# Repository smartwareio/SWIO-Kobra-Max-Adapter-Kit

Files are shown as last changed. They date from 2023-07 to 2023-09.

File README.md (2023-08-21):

# Welcome to the documentation for the SWIO Kobra Max Swap Kit. Here you will find information required to utilize the _Swap Board_ and _Extruder Board_ in the kit. Please note that this kit is currently in BETA and is a _work in progress_.

**Found this page without knowing about the product? Get it [here](https://www.smartwareio.com/product/kobra-max-mainboard-and-print-head-kit/9)!**

## You will need:

- To purchase or print a set of adapter plates [See the STL section](https://github.com/smartwareio/SWIO-Kobra-Max-Adapter-Kit/tree/main/STL) **If you are self-printing adapters, you will also need heat-sets, which are linked**
- A pair of JST crimpers
- A set of JST-XH connectors and pins
- Some 20-22ga stranded wire. Ribbon cable that comes with Dupont kits is hit or miss here. For the heater jumper, we recommend that you use 20-22AWG silicone (high heat) wire.
- _Optional, but recommended_: A ferrule crimper and ferrules for shortening or attaching multiple conductors together. You will likely need these for the cables on the NF103 bed heater board.

[**Recommended crimper and JST kit here** (Amazon)](https://amzn.to/3KvIH76)

[**Recommended cable for 2-wire connections here** (Amazon)](https://amzn.to/3Qx5LGw)

[**Recommended cable for 4-wire connections here** (Amazon)](https://amzn.to/3OPArBC)

[**Ferrule and crimper kit**](https://amzn.to/3qjfENh)

Start by selecting a board. **We recommend using the BTT SKR 3 EZ.** The pinout and wiring diagrams will be provided here.

Be sure to match GND to GND on your board for every connection. The Smartware boards are marked, but not all printer boards are. You will need to refer to the [_pin schedule_](https://github.com/bigtreetech/SKR-3/blob/master/Hardware%20(SKR%203%20EZ)/BIGTREETECH%20SKR%203%20EZ%20V1.0-PIN.pdf) for your particular board to ensure that this is correct. **Getting these wrong or reversed will result in errors and improper machine operation.**

Anycubic has reversed the stepper phase on the some motors for some Max printers. We have corrected for this in the adapter board, but your milage may vary here. If your stepper moves in the wrong direction, you will need to reverse one connector end for your motor. Our boards account for the Max we have available for development and have made all cables "striaght-through" style.

**The factory display is not going to work with this kit directly. There are mods that can be done, but we do not support them.**

### If you are using the factory strain gauge and omitting the Extruder Board:

- Install a logic level shifter such as the [Sparkfun BOB](https://amzn.to/3QuQJ40).
- See [Wiring the Swap Board](https://github.com/smartwareio/SWIO-Kobra-Max-Adapter-Kit/tree/main#wiring-the-swap-board) for instructions on how to use it.
- **Most shifters do not have mounting provisions as they are tiny. You can hot glue it or modify the board adapter plate to have some tabs for it if you wish.**
- **The level shifter is REQUIRED to be used with the factory print head. The factory head sends 5V out into the GPIO upon reset. The shifter brings this to safe levels.**

#### Wiring the Swap Board

- [FAN0 / FAN1](https://github.com/smartwareio/SWIO-Kobra-Max-Adapter-Kit/blob/main/installation/fans.md)
- [Heater (extruder)](https://github.com/smartwareio/SWIO-Kobra-Max-Adapter-Kit/blob/main/installation/heater.md)
- [Thermistor (extruder)](https://github.com/smartwareio/SWIO-Kobra-Max-Adapter-Kit/blob/main/installation/thermistor.md)
- [Z Optical](https://github.com/smartwareio/SWIO-Kobra-Max-Adapter-Kit/blob/main/installation/z_optical.md) (you may skip this if using Klipper)
- [Filament Runout Sensor](https://github.com/smartwareio/SWIO-Kobra-Max-Adapter-Kit/blob/main/installation/runout.md)
- [X Stop](https://github.com/smartwareio/SWIO-Kobra-Max-Adapter-Kit/blob/main/installation/xstop.md)
- [Y Stop](https://github.com/smartwareio/SWIO-Kobra-Max-Adapter-Kit/blob/main/installation/ystop.md)
- [E Motor](https://github.com/smartwareio/SWIO-Kobra-Max-Adapter-Kit/blob/main/installation/emotor.md)
- [X Motor](https://github.com/smartwareio/SWIO-Kobra-Max-Adapter-Kit/blob/main/installation/xmotor.md)
- [Y Motor](https://github.com/smartwareio/SWIO-Kobra-Max-Adapter-Kit/blob/main/installation/ymotor.md)
- [Z0 Motor, Z1 Motor](https://github.com/smartwareio/SWIO-Kobra-Max-Adapter-Kit/blob/main/installation/zmotors.md) (and special note)
- Factory Kobra Max connections
- [Factory strain gauge/toolhead & required Logic Level Shifter](https://github.com/smartwareio/SWIO-Kobra-Max-Adapter-Kit/blob/main/installation/shifter_printhead.md)
- Factory NF103 Heater Board

  ##### Printer Profiles

  - Check out the [Cura Project Files](https://github.com/smartwareio/SWIO-Kobra-Max-Adapter-Kit/tree/main/CuraProjectProfiles) folder for some premade profiles that we have been using and fine tuning for several months.

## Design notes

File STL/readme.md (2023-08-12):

# Links to printable models developed specifically for this project below.

[Kobra Max top mounted filament sensor bracket](https://than.gs/m/916912)

[Various bearing-driven spool holders, including two specifically for the Kobra Max (top mount, side mount)](https://than.gs/m/850530)

[Kobra Max adapter plates to mount the SKR3 and SWIO Swap/Extruder Boards](https://than.gs/m/917034)

## Models hosted here are going to be replaced with Thangs links, due to the easy ability to revision them and track downloads used.

The NF103 mount will slot the JST adapter board next to the NF103 (bed heater board). If you are using an SKR board (any SKR board), you may omit the NF103. If you DO install the NF103, be sure to print the spacer and put it between the board and mount. This is to prevent the mounting screws from hitting anything under the board.

All spacers are designed to take 2mm and 3mm heat-sets. You can check the DXF folder for the outlines and model your own without heat-sets, however this is not recommended for parts that generate heat/hold current carrying electronics.

Be sure to print these in a filament that can withstand the environmental temperatures you intend to run the printer in.

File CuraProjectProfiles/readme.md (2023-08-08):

# Here you will find Cura project files for the Kobra Max.

- Open into Cura 5.3+ and choose **Open as project**



- Choose **Create new** and then open the file.



- This will import a calibration cube onto the bed and load the profiles into the machine.



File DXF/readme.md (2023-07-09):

Here you will find DXF files to use as templates to create your own mounting plates/enclosures/solutions.

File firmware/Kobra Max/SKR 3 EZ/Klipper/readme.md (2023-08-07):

- [Stock Printhead](https://github.com/smartwareio/SWIO-Kobra-Max-Adapter-Kit/tree/main/firmware/Kobra%20Max/SKR%203%20EZ/Klipper/Stock%20Printhead) folder is for machines using the **Swap Board** and the **factory Anycubic print head assembly, including the strain gauge**.
- Other printhead folders are for machines using direct drives, touch probes, etc via the **Extruder Board**.
- The SKR 3 EZ has now shipped (confirmed) with two different CPUs. Please use the file for the CPU model that is written on _your particular_ mainboard.

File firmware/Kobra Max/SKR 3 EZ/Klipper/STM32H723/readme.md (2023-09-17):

klipper
v0.11.0-271-g5f990f93

Compiled for STM32H723 which is NOT the advertised CPU that the SKR 3 EZ comes with. Some 3 EZ boards are shipping with this CPU. This firmware is set for USB connection. If you need serial connection or CAN, you will need to use the make menuconfig and recompile.

Put the firmware.bin onto a BLANK SD card, 16GB or less. Do a quick format FAT32, copy the firmware.bin to the card. Eject the card and remove from your machine. Turn OFF your printer, insert the card, turn on the printer. Count to 5, turn the printer off and remove the card.

To confirm the firmware loaded, insert the SD back into your computer. The "firmware.bin" file should be renamed "FIRMWARE.CUR".

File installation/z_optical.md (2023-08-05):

# How to wire the Z Optical port and sensor

**This sensor is not used for Klipper**, however the connections were brought to the new board since the ribbon contains them. This gives you 3 spare wires and ports to use for _anything you wish_.
The connection terminates directly in front of the left Z motor. A 3-pin JST extension cable can be used in order to utilize this port for RGB LEDs or any 3-pin device if desired.



[Return to installation header](https://github.com/smartwareio/SWIO-Kobra-Max-Adapter-Kit#wiring-the-swap-board)

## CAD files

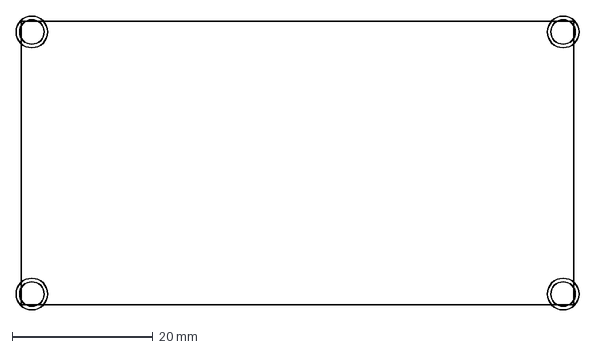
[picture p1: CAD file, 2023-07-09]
DXF/Mainboard Conversion Dimensions.dxf
80.0 x 41.8 mm

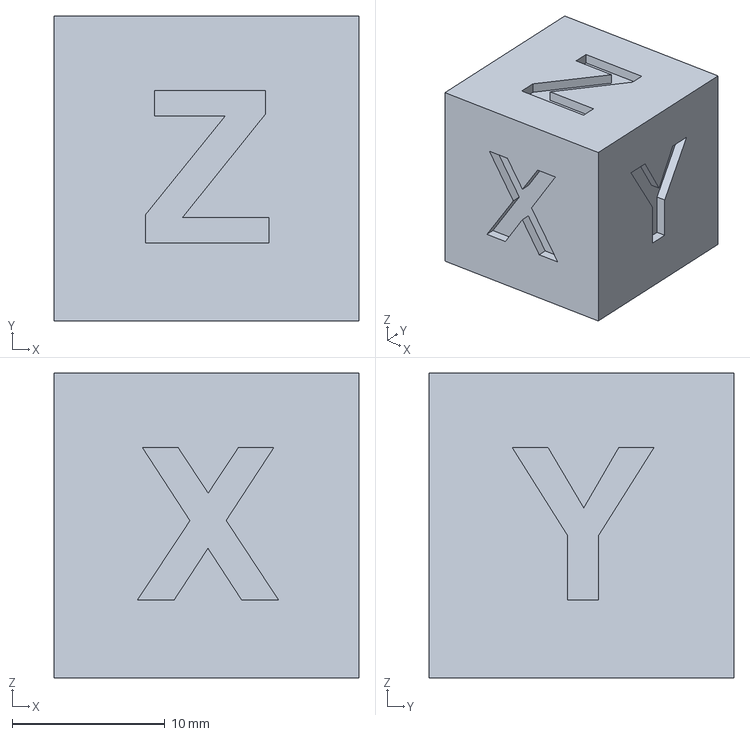
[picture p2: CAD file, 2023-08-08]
CuraProjectProfiles/StrainGauge-CookieCadPinkChip.3mf
20.0 x 20.0 x 20.0 mm

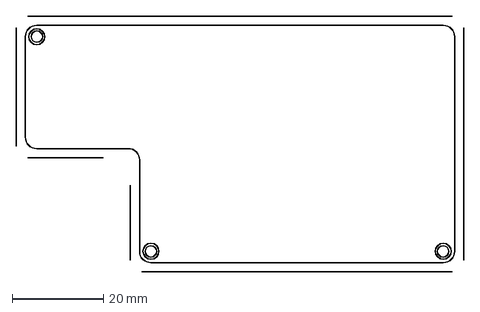
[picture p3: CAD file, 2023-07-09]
DXF/ExtruderBoard_Footprint.dxf
98.0 x 56.0 mm

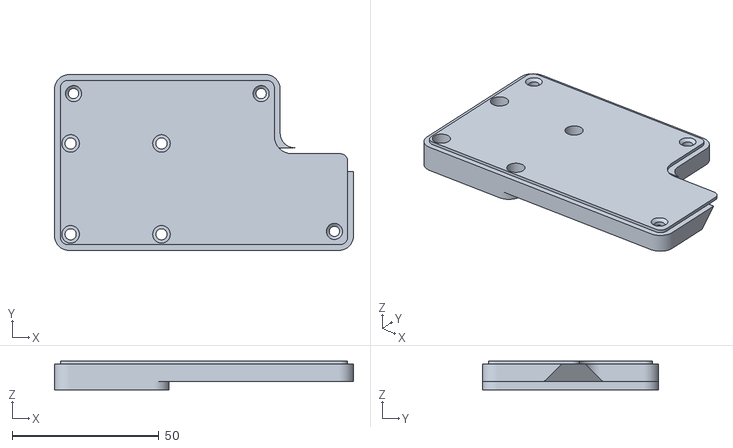
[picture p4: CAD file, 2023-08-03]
STL/ExtruderPCB_NoTop.stl
102.0 x 60.0 x 9.75

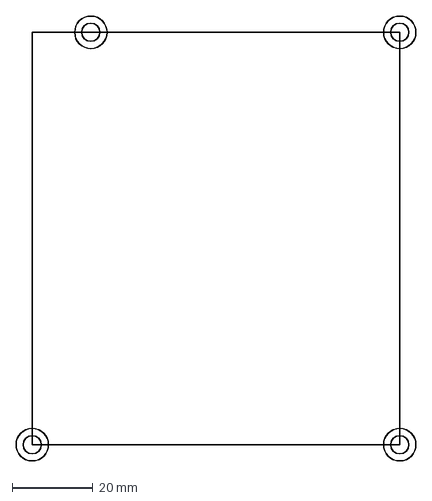
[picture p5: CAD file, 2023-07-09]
DXF/SKR3EZ_Footprint.dxf
98.8 x 109.9 mm

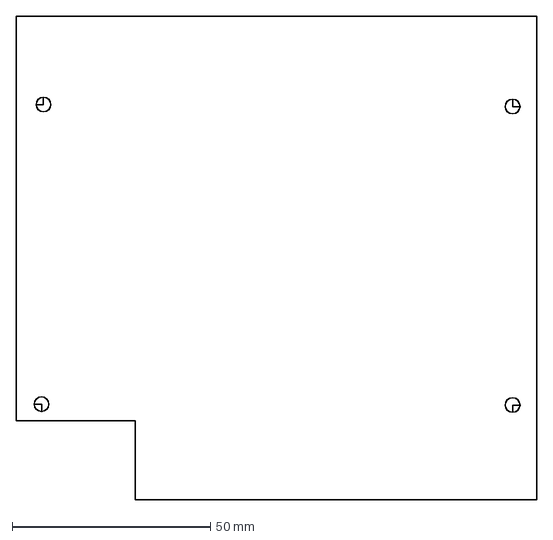
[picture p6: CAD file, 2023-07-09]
DXF/TrigorillaProA104_Footprint.dxf
131.3 x 122.1 mm

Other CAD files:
CuraProjectProfiles/StrainGauge-InlandPETG.3mf
CuraProjectProfiles/StrainGauge-PLA+06LineWidth.3mf

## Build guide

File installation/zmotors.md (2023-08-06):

# How to wire the Z Motors

From the **Swap Board** to the **SKR 3 EZ**:

## Wiring the first Z motor (Z0)
- Run a cable from Z0 1A to ZAM 1A
- Run a cable from Z0 1B to ZAM 1B
- Run a cable from Z0 2A to ZAM 2A
- Run a cable from Z0 2B to ZAM 2B

### Wiring the second Z motor (Z1)
- **Yes, the _E1M_ port is correct.** You are using the second (unused) extruder port as a 5th Z stepper driver. Using _ZBM_ just uses 1 driver for both Z ports, so Z_TILT will not function.
- Run a cable from Z1 1A to E1M 1A
- Run a cable from Z1 1B to E1M 1B
- Run a cable from Z1 2A to E1M 2A
- Run a cable from Z1 2B to E1M 2B



#### If you are using Klipper and the provided firmware, wiring in this manner will both support AND enable "Z_TILT".
- Loosen the bearing retainers at the top of the frame
- Loosen the Z sync belt couplers at the top
- Gently pop off the belt and set it aside; do not reinstall it. Reasssemble the top side, leaving the GT2 cogs in place.
- The printer will now sync the Z motors more accurately and perform additional tramming operations.

##### Some Z motors from Anycubic have a reversed phase. The Swap Board kit accounts for this in order to correct it and standardize all motor cable pinouts across the machine. If however, you find that your motor is moving in the opposite direction, reverse one end of the connector.

[Return to installation header](https://github.com/smartwareio/SWIO-Kobra-Max-Adapter-Kit/blob/main/README.md#wiring-the-swap-board)

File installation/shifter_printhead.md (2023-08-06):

# How to wire the Logic Level Shifter and factory print head

From the **BOB 12009** to the **SKR 3 EZ**:
- Run a wire from HV to Z-Stop +5V. _This supplies a 5V reference to the shifter chip._
- Run a wire from GND to GND. _(jump the two grounds together)_
- Run a wire from GND to Z-Stop GND. _This allows the shifter to reference mainboard ground._
- Run a wire from LV to Z-Stop PC0. _This pin is set to 3.3V in the SWIO Config File and allows the shifter to supply 3.3V when 5V from the strain gauge is sent out._
- Run a wire from LV1 to PROBE PC13.
- **You will skip using the PROBE GND connection on the SKR. The shifter is providing ground reference.**

From the **BOB 12009** to the **Swap Board**:
- Run a wire from HV1 to PRB

From the **Swap Board** to the **SKR 3 EZ**:
- Run a wire from PRBRST to SERVO PE5. _This is the pin that resets the strain gauge._
- Run a wire from 5V to SERVO +5V. _This is the pin that powers the toolhead components._
- Run a wire from GND to SERVO GND. _This is the ground reference for the toolhead._
- Run a wire from LED to RGB PE6. _You will not use the other pins on RGB._



[Return to installation header](https://github.com/smartwareio/SWIO-Kobra-Max-Adapter-Kit/tree/main#wiring-the-swap-board)

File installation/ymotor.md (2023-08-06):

# How to wire the Y Motor

From the **Swap Board** to the **SKR 3 EZ**:

- Run a cable from Y1A to YM 1A
- Run a cable from Y1B to YM 1B
- Run a cable from Y2A to YM 2A
- Run a cable from Y2B to YM 2B



## Some Y motors from Anycubic have a reversed phase. The Swap Board kit accounts for this in order to correct it and standardize all motor cable pinouts across the machine. If however, you find that your motor is moving in the opposite direction, reverse one end of the connector.

[Return to installation header](https://github.com/smartwareio/SWIO-Kobra-Max-Adapter-Kit/blob/main/README.md#wiring-the-swap-board)

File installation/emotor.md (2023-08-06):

# How to wire the E Motor

From the **Swap Board** to the **SKR 3 EZ**:

- Run a cable from E1A to E0M 1A
- Run a cable from E1B to E0M 1B
- Run a cable from E2A to E0M 2A
- Run a cable from E2B to E0M 2B



## Some E motors from Anycubic have a reversed phase. The Swap Board kit accounts for this in order to correct it and standardize all motor cable pinouts across the machine. If however, you find that your motor is moving in the opposite direction, reverse one end of the connector.

[Return to installation header](https://github.com/smartwareio/SWIO-Kobra-Max-Adapter-Kit/blob/main/README.md#wiring-the-swap-board)

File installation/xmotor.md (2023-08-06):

# How to wire the X Motor

From the **Swap Board** to the **SKR 3 EZ**:

- Run a cable from X1A to XM 1A
- Run a cable from X1B to XM 1B
- Run a cable from X2A to XM 2A
- Run a cable from X2B to XM 2B



## Some X motors from Anycubic have a reversed phase. The Swap Board kit accounts for this in order to correct it and standardize all motor cable pinouts across the machine. If however, you find that your motor is moving in the opposite direction, reverse one end of the connector.

[Return to installation header](https://github.com/smartwareio/SWIO-Kobra-Max-Adapter-Kit/blob/main/README.md#wiring-the-swap-board)

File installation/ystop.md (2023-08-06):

# How to wire the Y-Stop

From the **Swap Board** to the **SKR 3 EZ**:

- Run a cable from YSTOP GND to Y-STOP GND
- Run a cable from YSTOP I/O to Y-STOP PC3



[Return to installation header](https://github.com/smartwareio/SWIO-Kobra-Max-Adapter-Kit/blob/main/README.md#wiring-the-swap-board)

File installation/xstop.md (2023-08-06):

# How to wire the X-Stop

From the **Swap Board** to the **SKR 3 EZ**:

- Run a cable from XSTOP GND to X-STOP GND
- Run a cable from XSTOP I/O to X-STOP PC1



[Return to installation header](https://github.com/smartwareio/SWIO-Kobra-Max-Adapter-Kit/blob/main/README.md#wiring-the-swap-board)

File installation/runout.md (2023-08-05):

# How to wire the filament runout sensor
_Please note that there will be two ways to go about this_. If you are using the factory print head and have only swapped the mainboard, you will only be connecting to the **Swap Board**.
If you are using both the **Swap Board** _and_ the **Extruder Board**, you will need to run a new length of cable directly from the SKR to the top of your frame. This is because the runout sensor in the factory location will no longer work for you, and you have converted to Direct Drive.

## "I am reusing the factory Kobra Max Print head":

From the **Swap Board** to the **SKR 3 EZ**:

- Run a wire from FLMT GND to E0DET GND
- Run a wire from FLMT I/O to E0DET PC2



### "I am using the Extruder Board for a direct drive conversion":

- Do not wire your sensor to the swap board. Wire it directly to the mainboard ports. As a bonus, you now have 3 wires to use and can have an LED on the sensor (utilize the 5V pin).
- Wire a 3 conductor length of wire and run it up the right frame support to the top of the frame. You will find a printable file to use a standard filament sensor up top.



[Return to installation header](https://github.com/smartwareio/SWIO-Kobra-Max-Adapter-Kit#wiring-the-swap-board)

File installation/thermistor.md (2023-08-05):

# How to wire the extruder thermistor

From the **Swap Board** to the **SKR 3 EZ**:

- Run a wire from T0 GND to TH0 GND on the SKR 3 EZ.
- Run a wire from T0 I/O to TH0 PA2 on the SKR 3 EZ.



[Return to installation header](https://github.com/smartwareio/SWIO-Kobra-Max-Adapter-Kit#wiring-the-swap-board)

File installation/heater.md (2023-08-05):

# How to wire the Heater Cartridge

From the **Swap Board** to the **SKR 3 EZ**:

- Terminate a _high heat_ silicone wire to HEAT +, run it to E0 VBB on the SKR 3 EZ.
- Terminate a _high heat_ silicone wire to HEAT I/O, run it to E0 PB3 on the SKR 3 EZ.



[Return to installation header](https://github.com/smartwareio/SWIO-Kobra-Max-Adapter-Kit#wiring-the-swap-board)

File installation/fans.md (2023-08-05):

# How to wire the factory fans

From the **Swap Board** to the **SKR 3 EZ**:

- Run a cable from FAN0 + to FAN0 VFAN
- Run a cable from FAN1 + to FAN1 VFAN
- Run a cable from FAN0 I/O to FAN0 PB7
- Run a cable from FAN1 I/O to FAN1 PB6
- Plug your factory mainboard fan into FAN2



[Return to installation header](https://github.com/smartwareio/SWIO-Kobra-Max-Adapter-Kit/blob/main/README.md#wiring-the-swap-board)

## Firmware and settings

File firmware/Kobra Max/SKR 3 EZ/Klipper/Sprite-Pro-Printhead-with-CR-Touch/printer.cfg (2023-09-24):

# This file contains common pin mappings for the BigTreeTech SKR 3 EZ.
# To use this config, the firmware should be compiled for the
# CPU in your SKR with a "128KiB bootloader".

# See docs/Config_Reference.md for a description of parameters.

### Enable this to use an RP2040 for your ADXL host. You cannot use the Orange Pi so this is the next best option.

#[mcu adxl]
# Change <mySerial> to whatever you found above. For example,
# usb-Klipper_rp2040_E661640843545B2E-if00
#serial: /dev/serial/by-id/usb-Klipper_rp2040_E660C062137B4E29-if00
#[adxl345]
#cs_pin: adxl:gpio1
#spi_bus: spi0a
#axes_map: x,z,y
#[resonance_tester]
#accel_chip: adxl345
#probe_points: 208.5, 214, 100
#[output_pin power_mode] # Improve power stability
#pin: adxl:gpio23

[mcu]
serial: /dev/serial/by-id/usb-Klipper_stm32h723xx_100030001651313238353730-if00
baud: 250000

[include mainsail.cfg]
[include macros.cfg]

## This is for CrydTeam's automatic accel and velocity testing, comment it out if you don't want to set it up.
## https://github.com/cryd-s/klipper_scripts/tree/main/speed_accel_script
[include speed_test.cfg]

## Enable M118 Echo
[respond]

## Enable cancelling individual objects in a print
## See https://www.obico.io/blog/klipper-exclude-object/#exclude-objects-feature
[exclude_object]

[stepper_x]
step_pin: PD4
dir_pin: PD3
enable_pin: !PD6
microsteps: 64
rotation_distance: 40
endstop_pin: !PC1
position_min: -7
position_endstop: -7
position_max: 417
homing_speed: 100

[tmc2209 stepper_x]
uart_pin: PD5
run_current: 0.850
#diag_pin:
stealthchop_threshold: 999999

[stepper_y]
step_pin: PA15
dir_pin: !PA8
enable_pin: !PD1
microsteps: 64
rotation_distance: 40
endstop_pin: !PC3
position_min: 0
position_endstop: 0
position_max: 428
homing_speed: 100

[tmc2209 stepper_y]
uart_pin: PD0
run_current: 0.950
#diag_pin:
stealthchop_threshold: 999999

[stepper_z]
step_pin: PE2
dir_pin: PE3
enable_pin: !PE0
microsteps: 16
rotation_distance: 8
endstop_pin: probe:z_virtual_endstop
position_min: -20
position_max: 452
homing_speed: 20

[tmc2209 stepper_z]
uart_pin: PE1
run_current: 0.850
#diag_pin:
stealthchop_threshold: 999999

[stepper_z1]
step_pin: PD11
dir_pin: PD10
enable_pin: !PD13
microsteps: 16
rotation_distance: 8
endstop_pin: probe:z_virtual_endstop

[tmc2209 stepper_z1]
uart_pin: PD12
run_current: 0.850
#diag_pin:
stealthchop_threshold: 999999

### Don't forget to SET YOUR E-STEPS!
### Measure 120mm, then extrude 100mm
### G1 E100 F100
### step_distance = old_e_steps * ((120 - distance_to_mark) / 100)

[extruder]
step_pin: PD15
dir_pin: PD14
enable_pin: !PC7
microsteps: 16
rotation_distance: 7.21
nozzle_diameter: 0.800
filament_diameter: 1.750
heater_pin: PB3
sensor_type: EPCOS 100K B57560G104F
sensor_pin: PA2
#control: pid
#pid_kp: 28.130
#pid_ki: 1.875
#pid_kd: 105.487
rotation_distance: 7.4088
nozzle_diameter: 0.800
filament_diameter: 1.750
min_temp: -77
max_temp: 300
max_extrude_only_distance: 100.0

[tmc2209 extruder]
uart_pin: PC6
run_current: 0.650
#diag_pin:
stealthchop_threshold: 999999

## This is for using a CR-Touch and the Smartware/IO Extruder Board
## This particular configuration is for a Sprite Pro harness. You may need to redo this if you are not using a CR-Touch.
## Please note the factory Extruder Board pins are not compatible with the CR-Touch. You will need to repin your CR-Touch connector.

[bltouch]
sensor_pin: ^PC13
control_pin: PE5
#z_offset: 4
speed: 20
samples: 2
pin_move_time: .680
sample_retract_dist: 3
probe_with_touch_mode: True
stow_on_each_sample: False
x_offset: -31.5
y_offset: -42

[safe_z_home]
home_xy_position: 208.5, 214 # Center of bed
speed: 100
z_hop: 5               # Move up 5mm
z_hop_speed: 20
move_to_previous: False

[bed_mesh]
speed: 100
horizontal_move_z: 4
mesh_min: 8.5, 13
mesh_max: 385.5, 386
algorithm: bicubic
probe_count: 5, 5

[z_tilt]
z_positions: 68.5, 254
            400.5, 254
points: 68.5, 254
        235, 254
        400.5, 254
speed: 250
retries: 10
retry_tolerance: 0.14

[filament_switch_sensor runout]
pause_on_runout: True
switch_pin: PC2
# use PC2 for aftermarket, !PC2 for stock sensor

## Don't turn off Z or bed heat during idle

[idle_timeout]
gcode:
  SET_HEATER_TEMPERATURE HEATER=extruder TARGET=0
timeout: 900

[heater_bed]
heater_pin: PD7
sensor_type: EPCOS 100K B57560G104F
sensor_pin: PA1
#control: watermark
min_temp: -77
max_temp: 130

[fan]
pin: PB7

[heater_fan hotend_fan]
pin: PB6
heater: extruder
heater_temp: 50.0

[controller_fan mcu_fan]
pin: PB5

[printer]
kinematics: cartesian
max_velocity: 250
max_accel: 3000
max_z_velocity: 5
max_z_accel: 100

[temperature_sensor pi_temp]
sensor_type: temperature_host
min_temp: 0
max_temp: 100

[temperature_sensor mcu_temp]
sensor_type: temperature_mcu
min_temp: 0
max_temp: 100

########################################
# EXP1 / EXP2 (display) pins
########################################

[board_pins]
aliases:
    # EXP1 header
    EXP1_1=PC5, EXP1_3=PB1, EXP1_5=PE9,  EXP1_7=PE11, EXP1_9=<GND>,
    EXP1_2=PB0, EXP1_4=PE8, EXP1_6=PE10, EXP1_8=PE12, EXP1_10=<5V>,
    # EXP2 header
    EXP2_1=PA6, EXP2_3=PE7, EXP2_5=PB2, EXP2_7=PC4,   EXP2_9=<GND>,
    EXP2_2=PA5, EXP2_4=PA4, EXP2_6=PA7, EXP2_8=<RST>, EXP2_10=<NC>

# See the sample-lcd.cfg file for definitions of common LCD displays.

#*# <---------------------- SAVE_CONFIG ---------------------->
#*# DO NOT EDIT THIS BLOCK OR BELOW. The contents are auto-generated.
#*#
#*# [heater_bed]
#*# pid_kp = 69.782
#*# pid_ki = 0.979
#*# pid_kd = 1242.996
#*# control = pid
#*#
#*# [extruder]
#*# control = pid
#*# pid_kp = 33.158
#*# pid_ki = 2.632
#*# pid_kd = 104.446
#*#
#*# [bltouch]
#*# z_offset = 1.970
#*#
#*# [input_shaper]
#*# shaper_type_x = mzv
#*# shaper_freq_x = 48.6
#*# shaper_type_y = 2hump_ei
#*# shaper_freq_y = 39.0

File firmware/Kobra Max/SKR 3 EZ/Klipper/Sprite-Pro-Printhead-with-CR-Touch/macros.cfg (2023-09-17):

#  Enable Marlin M600 command
[gcode_macro M600]
gcode:
    PAUSE

#     In CURA use the following machine Start GCODE:
#
#     START_PRINT EXTRUDER_TEMP={material_print_temperature_layer_0} BED_TEMP={material_bed_temperature_layer_0} AREA_START=%MINX%,%MINY% AREA_END=%MAXX%,%MAXY%
#
#     If you want to edit your Start Print GCODE, do it in this configuration instead.

[gcode_macro START_PRINT]
gcode:
    BED_MESH_CLEAR
    BED_MESH_PROFILE REMOVE="default"
    G92 E0; reset extruder
    G28; Home
    # Start preheating
    {% set BED_TEMP = params.BED_TEMP|default(70)|float %}
    {% set EXTRUDER_TEMP = params.EXTRUDER_TEMP|default(230)|float %}
    # Start bed heating (but don't wait for it)
    M140 S{BED_TEMP}
    # Use absolute coordinates
    G90
    # Wait for bed to reach temperature
    M190 S{BED_TEMP}
    # Set and wait for nozzle to reach temperature
    Z_TILT_ADJUST
    BED_MESH_CALIBRATE AREA_START={params.AREA_START|default("0,0")} AREA_END={params.AREA_END|default("0,0")}
    BED_MESH_PROFILE LOAD="default"
    M109 S{EXTRUDER_TEMP}
    PAUSE
    G1 Z25; Raise Z for blob time
    G0 E25 F300; spit out a pile of goo into the corner
    G92 E0; reset extruder
    G90

###     In CURA use the following machine End GCODE:
###
#     END_PRINT
###
###     If you want to edit your End Print GCODE, do it in this configuration instead.

[gcode_macro END_PRINT]
gcode:
    G92 E0; reset extruder
    G91
    #turn off heaters
    M106 S0
    M104 S0
    M140 S0
    G0 E-4 F2700; retract 4mm
    G1 E-2 Z0.2 F2400; retract 2mm more and raise Z by one layer
    G1 X5 Y5 F3000; move over 5mm for a wipe
    G1 Z10; raise Z by 10
    G90
    G1 X10 Y400; present the print
    M84 X Y E; turn off all the steppers but Z
    G92 E0; reset extruder

### This macro is to mesh only the area of the bed which will be printed on
### In order to take advantage of this option, there is further work you will need to do in your slicer software
### If you do not use Cura, please visit the following link to finish setting this up:
#
#                 https://gist.github.com/ChipCE/95fdbd3c2f3a064397f9610f915f7d02
#
### If you DO use Cura, I have already taken most steps for you. Please visit the following link to download the post processing plugin. Save this text as KlipperPrintArea.py.
#
#                 https://raw.githubusercontent.com/ChipCE/Slicer-profile/master/cura-slicer/scripts/KlipperPrintArea.py
#
### In cura menu Help -> Show configuration folder. - Copy the python script from the above link in to scripts folder. - Restart Cura - In cura menu Extensions ->
### Post processing -> Modify G-Code and select Klipper print area mesh


[gcode_macro BED_MESH_CALIBRATE]
rename_existing: BED_MESH_CALIBRATE_BASE
; gcode parameters
variable_parameter_AREA_START : 0,0
variable_parameter_AREA_END : 0,0
; the clearance between print area and probe area 
variable_mesh_area_offset : 5.0
; number of sample per probe point
variable_probe_samples : 2
; minimum probe count
variable_min_probe_count : 4
; scale up the probe count, should be 1.0 ~ < variable_max_probe_count/variable_min_probe_count
variable_probe_count_scale_factor : 1.0
; enable preference index
variable_enable_reference_index : False
gcode:
    {% if params.AREA_START and params.AREA_END %}
        {% set bedMeshConfig = printer["configfile"].config["bed_mesh"] %}
        {% set safe_min_x = bedMeshConfig.mesh_min.split(",")[0]|float %}
        {% set safe_min_y = bedMeshConfig.mesh_min.split(",")[1]|float %}
        {% set safe_max_x = bedMeshConfig.mesh_max.split(",")[0]|float %}
        {% set safe_max_y = bedMeshConfig.mesh_max.split(",")[1]|float %}

        {% set area_min_x = params.AREA_START.split(",")[0]|float %}
	{% set area_min_y = params.AREA_START.split(",")[1]|float %}
	{% set area_max_x = params.AREA_END.split(",")[0]|float %}
	{% set area_max_y = params.AREA_END.split(",")[1]|float %}

	{% if bedMeshConfig.probe_count.split(",")|length == 2 %}
            {% set meshPointX = bedMeshConfig.probe_count.split(",")[0]|int %}
            {% set meshPointY = bedMeshConfig.probe_count.split(",")[1]|int %}
        {% else %}
            {% set meshPointX = bedMeshConfig.probe_count.split(",")[0]|int %}
            {% set meshPointY = bedMeshConfig.probe_count.split(",")[0]|int %}
        {% endif %}

	{% set meshMaxPointX = meshPointX %}
	{% set meshMaxPointY = meshPointY %}


        {% if (area_min_x < area_max_x) and (area_min_y < area_max_y) %}
            {% if area_min_x - mesh_area_offset >=  safe_min_x %}
                {% set area_min_x = area_min_x - mesh_area_offset %}
            {% else %}
                {% set area_min_x = safe_min_x %}
            {% endif %}

            {% if area_min_y - mesh_area_offset >=  safe_min_y %}
                {% set area_min_y = area_min_y - mesh_area_offset %}
            {% else %}
                {% set area_min_y = safe_min_y %}
            {% endif %}

            {% if area_max_x + mesh_area_offset <=  safe_max_x %}
                {% set area_max_x = area_max_x + mesh_area_offset %}
            {% else %}
                {% set area_max_x = safe_max_x %}
            {% endif %}

            {% if area_max_y + mesh_area_offset <=  safe_max_y %}
                {% set area_max_y = area_max_y + mesh_area_offset %}
            {% else %}
                {% set area_max_y = safe_max_y %}
            {% endif %}

            {% set meshPointX = (meshPointX * (area_max_x - area_min_x) / (safe_max_x - safe_min_x) * probe_count_scale_factor)|round(0)|int %}
            {% if meshPointX < min_probe_count %}
                {% set meshPointX = min_probe_count %}
            {% endif %}
	    {% if meshPointX > meshMaxPointX %}
                {% set meshPointX = meshMaxPointX %}
            {% endif %}

            {% set meshPointY = (meshPointY * (area_max_y -area_min_y ) / (safe_max_y - safe_min_y) * probe_count_scale_factor )|round(0)|int %}
            {% if meshPointY < min_probe_count %}
                {% set meshPointY = min_probe_count %}
            {% endif %}
	    {% if meshPointY > meshMaxPointY %}
                {% set meshPointY = meshMaxPointY %}
            {% endif %}

            {% set algorithm = "bicubic" %}
	    {% if "algorithm" in bedMeshConfig %}
	        {% set algorithm = bedMeshConfig.algorithm %}
            {% endif %}
            {% if meshPointX >=7 or meshPointY >=7 %}
                {% set algorithm = "bicubic" %}
            {% endif %}

            {% if enable_reference_index %}
                {% set referenceIndex = (meshPointX * meshPointY / 2 - 1 )|round(0)|int %}
                BED_MESH_CALIBRATE_BASE mesh_min={area_min_x},{area_min_y} mesh_max={area_max_x},{area_max_y} probe_count={meshPointX},{meshPointY} samples={probe_samples|int} algorithm={algorithm} relative_reference_index={referenceIndex}
            {% else %}
                BED_MESH_CALIBRATE_BASE mesh_min={area_min_x},{area_min_y} mesh_max={area_max_x},{area_max_y} probe_count={meshPointX},{meshPointY} samples={probe_samples|int} algorithm={algorithm}
            {% endif %}
        {% else %}
            BED_MESH_CALIBRATE_BASE
        {% endif %}
    {% else %}
        BED_MESH_CALIBRATE_BASE
    {% endif %}


### This is the SPEED TEST MACRO written by Andrew Ellis (ellis3dp.com).
### Please read the documentation before torturing your printer with it!
#
#     https://ellis3dp.com/Print-Tuning-Guide/articles/determining_max_speeds_accels.html
#
### Home, get position, throw around toolhead, home again.
### If MCU stepper positions (first line in GET_POSITION) are greater than a full step different (your number of microsteps), then skipping occured.
### We only measure to a full step to accomodate for endstop variance.
### Example: TEST_SPEED SPEED=300 ACCEL=5000 ITERATIONS=10
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

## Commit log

2023-08-05 Rename firmware/Kobra Max/SKR 3 EZ/Klipper/macros.cfg to firmware/Kobra Max/SKR 3 EZ/Klipper/Stock Printhead/macros.cfg
    [macros.cfg]
2023-08-05 Rename firmware/Kobra Max/SKR 3 EZ/Klipper/moonraker.conf to firmware/Kobra Max/SKR 3 EZ/Klipper/Stock Printhead/moonraker.conf
2023-08-05 Rename firmware/Kobra Max/SKR 3 EZ/Klipper/printer.cfg to firmware/Kobra Max/SKR 3 EZ/Klipper/Stock Printhead/printer.cfg
    [printer.cfg]
